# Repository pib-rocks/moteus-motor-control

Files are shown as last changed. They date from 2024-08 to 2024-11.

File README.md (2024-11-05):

# Balancing Lower Body for pib

## Introduction

To aquire stable movement on the ground for pib, we created a wheel leg hybrid to achieve both; fast, energy efficient and manuevarbility of wheels and ability to squat and change posture of legs. For this system, balancing is a fundamental capability to enable stability. In this project, we focus on balancing the lower body of pib, using control algorithms applied to a simplified model of an inverted pendulum on a cart. By implementing control strategies like PID and LQR, we aim to keep the robot upright and stable while moving.

## MJbots MOTEUS

[Moteus](https://github.com/mjbots/moteus) is a high-performance servo motor controller designed by MJBots. It is ideal for robotic applications requiring precise motion control. Moteus offers advanced features such as torque, position, and velocity control, making it suitable for implementing sophisticated control algorithms needed for balancing tasks. We will be using R4.1 controller for this project to control 90kv eagle power brushless motor. The internal control loops for the motor is explained in [PID for motor](https://pib-rocks.atlassian.net/wiki/x/AQBGEg)

## Installation

Clone the repository and navigate to the balancing directory:

```
git clone https://github.com/pib-rocks/moteus-motor-control.git
cd moteus-motor-control/python/balancing
```
Install the required Python packages:
```
pip install -r requirements.txt
```

Configure the motors by running:
```
python3 settings.py
```

## Quick Scripts for LQR and PID Balancing

To quickly test the balancing algorithms on a 1 DOF inverted pendulum system (not on a cart), run the following scripts.
[PID 0 pitch](https://youtube.com/shorts/0coK8HC5Wkk?feature=share)
[LQR 0 pitch](https://youtube.com/shorts/olOWUviZS1A?feature=share)

### PID Balancing

```bash
python3 pid_balancing.py
```

### LQR Balancing

```bash
python3 lqr_balancing.py
```

## Balancing System Explanation

The balancing system models the lower body of PIB as an inverted pendulum mounted on a cart. The cart represents the wheel base, and the pendulum represents the robot's torso. The objective is to apply control inputs to the motors (cart) to keep the pendulum (robot) balanced upright. This setup simplifies the complex dynamics of a humanoid robot to a more manageable control problem. The goal is to keep angular pitch velcoity at 0 and pitch angle upright. To achieve this we are using Tinkerforge IMU bricklet to provide orientation and angular velocity feedback.

## PID Balancing

### PID Controller Explanation
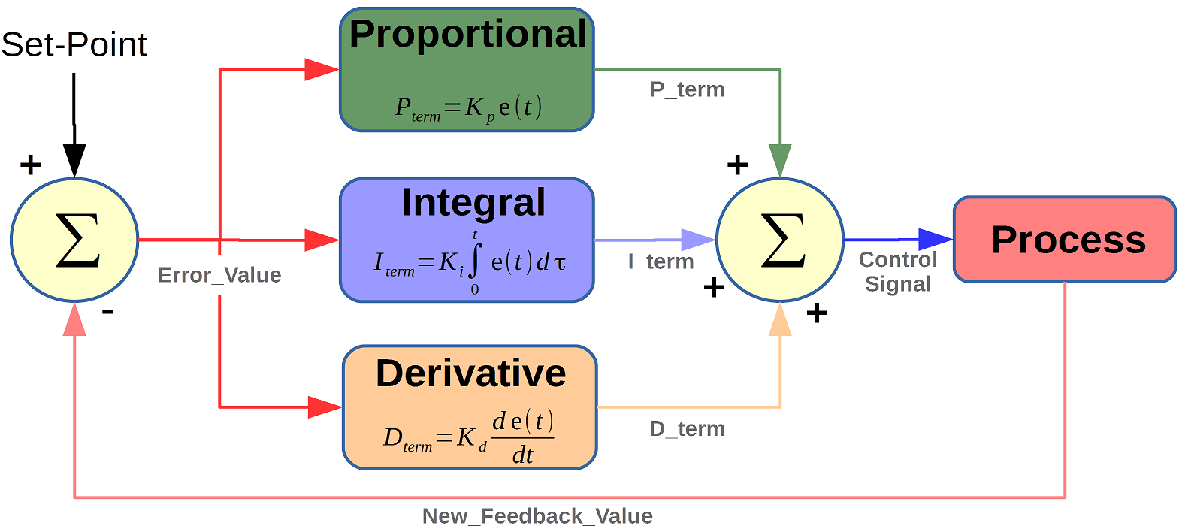
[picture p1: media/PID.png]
PID diagram

A PID controller computes an error value as the difference between a desired setpoint and a measured process variable. It applies a correction based on proportional (P), integral (I), and derivative (D) terms. In our case, we use a PD controller (proportional and derivative terms only) to balance the inverted pendulum.

The control input \( u(t) \) is calculated as:

$$
u(t) = K_p e(t) + K_d \frac{{de(t)}}{{dt}}
$$

- e(t): Error between the desired angle (upright position) and the current angle.
- Kp: Proportional gain.
- Kd: Derivative gain.

The proportional term adjusts the control input proportional to the error, while the derivative term predicts system behavior, providing damping and improving stability. With PID we are running one loop to minimize angular pitch angle to zero by doing velocity control.
videos
[Disturbance compensation with PID](https://youtube.com/shorts/M5Nd9FfMVe8?feature=share)

### Running the PID Script

Execute the PD balancing script:

```bash
python3 pid_balancing.py
```

Ensure that the gains \( K_p \) and \( K_d \) are properly tuned in the script for optimal performance.

## System Dynamics

The inverted pendulum on a cart can be described by the following equations of motion:

$$
m \ddot{x} + m l \ddot{\theta} \cos \theta - m l \dot{\theta}^2 \sin \theta = F
$$

$$
m l \ddot{x} \cos \theta + m l^2 \ddot{\theta} - m g l \sin \theta = 0
$$

Where:
- x: Position of the cart.
- theta: Angle of the pendulum (from vertical).
- m: Mass of the pendulum.
- l: Length to the pendulum's center of mass.
- F: Force applied to the cart.
- g: Acceleration due to gravity.
These nonlinear equations describe the coupling between the cart and pendulum dynamics.

## State-Space Representation

Linearizing the system around the upright position (\( \theta \approx 0 \)), we obtain the state-space representation:
Inverted pendulum cart
$$
\dot{\mathbf{x}} = A \mathbf{x} + B u
$$

$$
\mathbf{y} = C \mathbf{x} + D u
$$

State vector:

$$
\mathbf{x} = \begin{bmatrix} x \\ \dot{x} \\ \theta \\ \dot{\theta} \end{bmatrix}
$$

Input vector:

$$
u = F
$$

System matrices:

$$
A = \begin{bmatrix}
0 & 1 & 0 & 0 \\
0 & 0 & -\frac{m g}{M} & 0 \\
0 & 0 & 0 & 1 \\
0 & 0 & \frac{(M + m) g}{M l} & 0
\end{bmatrix}, \quad
B = \begin{bmatrix}
0 \\
\frac{1}{M} \\
0 \\
-\frac{1}{M l}
\end{bmatrix}
$$

Where:
- M: Mass of the cart.
- m: Mass of the pendulum.
- l: Length to the pendulum's center of mass.
- g: Acceleration due to gravity.
This linearized model is used for designing the LQR controller.

## LQR Balancing

### LQR Controller Explanation
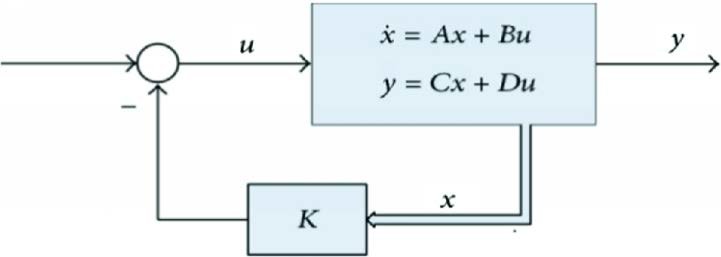
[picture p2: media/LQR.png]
LQR diagram

The Linear Quadratic Regulator (LQR) is an optimal control strategy that minimizes a cost function representing the trade-off between state error and control effort. The cost function is defined as:

$$
J = \int_{0}^{\infty} (\mathbf{x}^\top Q \mathbf{x} + u^\top R u) \, dt
$$

- Q: State weighting matrix (positive semi-definite).
- R: Control input weighting scalar or matrix (positive definite).
- \mathbf{x} \): State vector.
- u: Control input.

The optimal state-feedback gain matrix \( K \) is computed by solving the Continuous-Time Algebraic Riccati Equation (CARE):

$$
A^\top P + P A - P B R^{-1} B^\top P + Q = 0
$$

$$
K = R^{-1} B^\top P
$$

Where \( P \) is the solution to the CARE. The control law becomes:

u = -Kx

[Disturbance compensation with LQR](https://youtube.com/shorts/rGGWK-xfWDU?feature=share)
### Running the LQR Script

Execute the LQR balancing script:

```bash
python3 lqr_balancing.py
```

Ensure that the Q and R matrices are appropriately chosen in the script to balance performance and control effort. Proper tuning of these matrices is crucial for achieving optimal balancing behavior. For simplicity, in the current script there is a variable named "scale_factor" that should be adjusted to scale control output.

## References

- [Josh Pieper: Hoverbot - Hoverboard Motor Balancing Robot](https://youtu.be/syxE1NEU7lw?feature=shared&t=449)

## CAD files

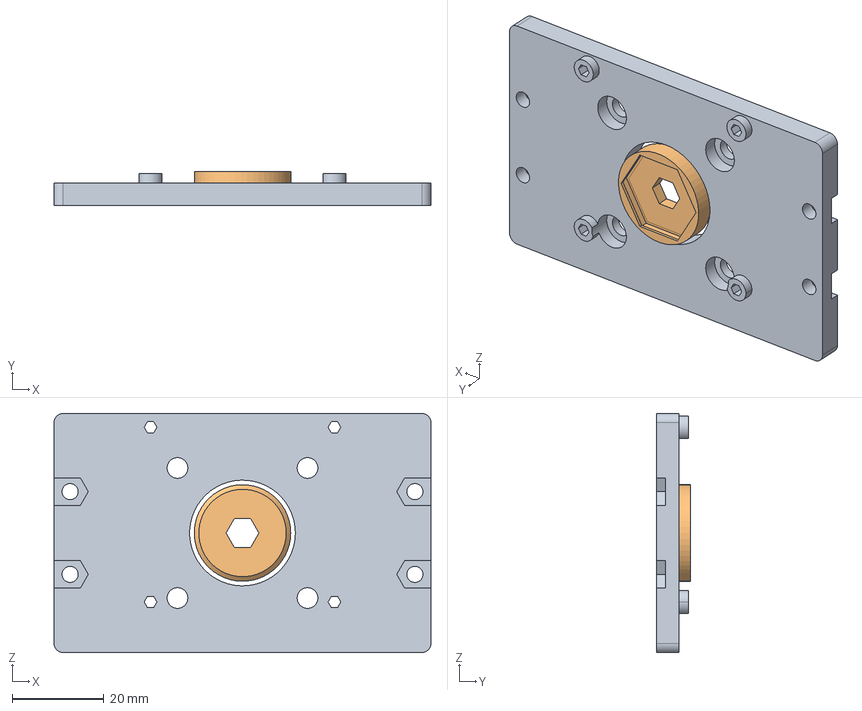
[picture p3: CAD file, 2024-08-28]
freecad/motor-stand/motor-plate.FCStd
82.0 x 7.50 x 52.0 mm
Cap

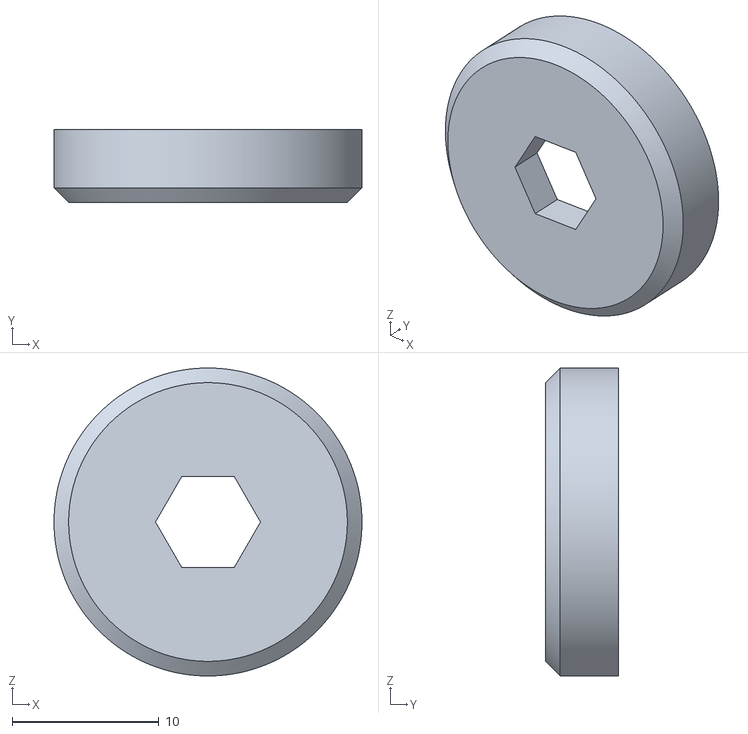
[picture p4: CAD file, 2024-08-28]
freecad/motor-stand/motor-plate-Cap.stl
21.0 x 5.00 x 21.0

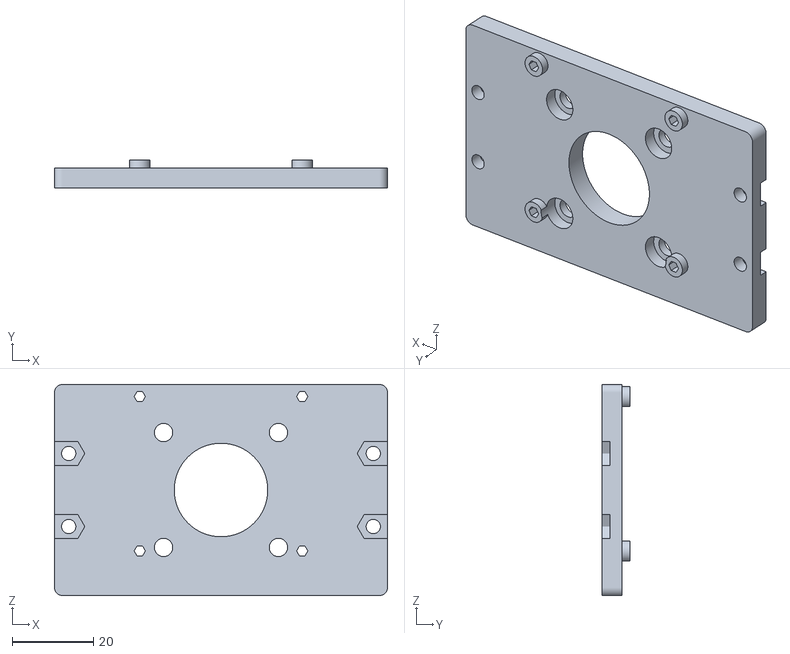
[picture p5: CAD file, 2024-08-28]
freecad/motor-stand/motor-plate-Body.stl
82.0 x 7.00 x 52.0

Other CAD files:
freecad/motor-stand/motor-plate.3mf

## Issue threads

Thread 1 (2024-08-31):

improved parameters for eaglepower direct drive with velocity mode

jnweiger, 2024-08-31:
```
                jw, Sa 31. Aug 17:39:44 CEST 2024

use moteus tview
================

tview -d 1,2 &          # start the gui for motors 1 & 2
# enter velocity mode:
d pos nan 0.5 10 v0.5                   # start rotating slowly 0.5 Hz, with up to 10Nm torque
d pos nan -1 10 v1 a0.5                 # start rotating slowly at 1 Hz backwards, 10 Nm, and accelerate slowly.
conf set servo.max_position_slip 0      # 0 always stops the motor
conf set servo.max_position_slip 1      # allows up to 1 revolution error before we get servo.fault=33 and the motor stops.
conf set servo.max_position_slip nan    # allows up to 1 revolution error before we get servo.fault=33 and the motor stops.
                                        # this depends on the drive direction?? It did not trigger with v=-0.5 ??
d stop && d pos nan -1 10               # clear servo.fault and continue velocity mode.

velocity mode according to video https://youtu.be/dG4fPKN0bas
-------------------------------------------------------------
# do the following for both motors, in the gui, prefix with "1>" (default) and then again with "2>"
conf set servo.max_position_slip 0.2            # unit: revolutions.
                                                #  it only works reliable with non.
conf set servopos.position_max nan
conf set servopos.position_min nan
conf set servo.pid_position.kp 4                # default
conf set servo.pid_position.kd .15              # was 0.04...   .5 also still nice. no overshoot!
conf set servo.pid_position.ki 1                # was 1, not much effect between 0 and 99

conf set servo.default_velocity_limit   ...
conf get servo.default_accel_limit
        5.0
conf set servo.default_accel_limit .5           # so that we can ommit a0.5 from the d pos nan command
# conf limited maximum torque  ? how?
conf set servo.max_position_slip .5             # much stronger torque than with 0.2
#conf set servo.max_position_slip .9            # stronger torque than 0.5, but significant speed overshoot.
conf set servo.max_velocity_slip 9              # unit Hz.

# plot values
servostats.velocity             "measured velocity"
servostats.control_velocity     "internally interpolated velocity that obeys any effective accerlation or velocity limits"
servo_cmd.velocity              "instantaneously updated as commands come in"

conf set servo.pid_position.kp 100              # much stronger
conf set servo.pid_position.kd 3                # 10 rattles
#conf set servo.max_position_slip .1            # good. with kp 100 and kd 3

# emergency stop from the command line:
python3 -m moteus.moteus_tool --target 1 -s

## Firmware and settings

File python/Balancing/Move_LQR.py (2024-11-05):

import asyncio
import time
from tinkerforge.ip_connection import IPConnection
from tinkerforge.bricklet_imu_v3 import BrickletIMUV3
from moteus import Controller
import math
import numpy as np
import control as ct
import threading
import sys

# For keyboard input
import tty
import termios

HOST = "localhost"
PORT = 4223
UID = "2bS8"  # Replace UID

# Global variable for user input
user_velocity = 0.0
user_turn = 0.0

def keyboard_input():
    global user_velocity, user_turn
    # Set terminal to raw mode
    fd = sys.stdin.fileno()
    old_settings = termios.tcgetattr(fd)
    tty.setraw(fd)
    
    try:
        while True:
            key = sys.stdin.read(1)
            if key == 'w':
                user_velocity += 0.1  # Increase forward speed
            elif key == 's':
                user_velocity -= 0.1  # Decrease forward speed
            elif key == 'a':
                user_turn += 0.1      # Turn left
            elif key == 'd':
                user_turn -= 0.1      # Turn right
            elif key == 'q':
                break  # Exit the loop on 'q' key
            else:
                pass  # Ignore other keys
            # Limit the user_velocity and user_turn
            user_velocity = max(min(user_velocity, 1.0), -1.0)
            user_turn = max(min(user_turn, 0.5), -0.5)
    finally:
        # Restore terminal settings
        termios.tcsetattr(fd, termios.TCSADRAIN, old_settings)

async def main():
    global user_velocity, user_turn
    ipcon = IPConnection()
    imu = BrickletIMUV3(UID, ipcon)
    ipcon.connect(HOST, PORT)

    # Initialize controllers
    controller_left = Controller(id=1)
    controller_right = Controller(id=2)

    # System parameters for inverted pendulum on cart
    M = 0.5   # Mass of the cart (kg)
    m = 0.2   # Mass of the pendulum (kg)
    b = 0.1   # Coefficient of friction for cart (N/m/sec)
    I = m * l**2 # Mass moment of inertia of the pendulum (kg*m^2)
    g = 9.81  # Gravity acceleration (m/s^2)
    l = 0.3   # Length to pendulum center of mass (m)

    # Denominator for the A and B matrices
    denom = I*(M+m) + M*m*l**2

    # State-space representation
    A = np.array([
        [0, 1, 0, 0],
        [0, -(I + m * l**2) * b / denom, (m**2 * g * l**2) / denom, 0],
        [0, 0, 0, 1],
        [0, -(m * l * b) / denom, m * g * l * (M + m) / denom, 0]
    ])

    B = np.array([
        [0],
        [(I + m * l**2) / denom],
        [0],
        [m * l / denom]
    ])

    # LQR weighting matrices
    Q = np.diag([10, 1, 10, 1])
    R = np.array([[0.1]])

    # Compute LQR gain
    K, _, _ = ct.lqr(A, B, Q, R)

    # Scale factor to map control input to motor command
    scale_factor = 0.05  # Adjust as necessary

    # Deadband thresholds
    deadband_angle_deg = 0.5  # degrees

    # Start keyboard input thread
    input_thread = threading.Thread(target=keyboard_input)
    input_thread.daemon = True
    input_thread.start()

    print("Starting balancing robot with LQR control and keyboard input. Press 'q' to exit.")

    try:
        while True:
            # Read IMU orientation (pitch angle) and angular velocity
            try:
                _, _, pitch = imu.get_orientation()
                pitch_angle_deg = (pitch / 100.0)*6.3  # Pitch angle in degrees
                pitch_angle_rad = math.radians(pitch_angle_deg)  # Convert to radians

                angular_velocity_x, _, _ = imu.get_angular_velocity()
                # Angular velocity around x-axis (pitch rate), in degrees per second
                pitch_rate_deg_per_sec = angular_velocity_x / 16.0
                pitch_rate_rad_per_sec = math.radians(pitch_rate_deg_per_sec)

                # Assume x and x_dot can be approximated from wheel encoders
                # For simplicity, we set x and x_dot to zero (you can implement odometry here)
                x_pos = 0.0
                x_dot = (controller_left.state.velocity + controller_right.state.velocity) / 2.0
            except Exception as e:
                print(f"Error reading sensors: {e}")
                continue

            # Form state vector x
            x = np.array([
                [x_pos],
                [x_dot],
                [pitch_angle_rad],
                [pitch_rate_rad_per_sec]
            ])

            # Desired state (setpoints)
            x_desired = np.array([
                [0.0],                # Desired position (you can set this to control position)
                [user_velocity],      # Desired velocity (from user input)
                [0.0],                # Desired pitch angle (upright)
                [0.0]                 # Desired pitch rate
            ])

            # Compute control input u using LQR
            u = -K @ (x - x_desired)

            # Extract scalar control input
            command = float(u[0, 0]) * scale_factor


            # Adjust for turning
            left_command = command + user_turn
            right_command = command - user_turn

            # Logging for debugging
            current_time = time.time()
            if int(current_time * 10) % 1 == 0:
                print(f"Pitch Angle: {pitch_angle_deg:.2f}°, Command: {command:.2f}, Left Cmd: {left_command:.2f}, Right Cmd: {right_command:.2f}")

            # Send velocity commands to the motors
            try:
                await controller_left.set_position(
                    position=math.nan,
                    velocity=left_command,
                    velocity_limit=2,
                    maximum_torque=1,
                    kp_scale=1,
                    kd_scale=12
                )
                await controller_right.set_position(
                    position=math.nan,
                    velocity=right_command,
                    velocity_limit=2,
                    maximum_torque=1,
                    kp_scale=1,
                    kd_scale=12
                )
            except Exception as e:
                print(f"Error sending commands to motors: {e}")
                continue

            # Small delay to prevent high CPU usage
            await asyncio.sleep(0.01)

    except KeyboardInterrupt:
        print("Stopping robot...")
    except Exception as e:
        print(f"An unexpected error occurred: {e}")
    finally:
        try:
            await controller_left.set_stop()
            await controller_right.set_stop()
        except Exception as e:
            print(f"Error stopping motors: {e}")
        ipcon.disconnect()

if __name__ == "__main__":
    asyncio.run(main())

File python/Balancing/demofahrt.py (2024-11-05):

#! /usr/bin/python3
#
# References:
#       https://github.com/mjbots/moteus/blob/main/docs/reference.md#velocity-control

import sys
import asyncio
import math
import moteus
import argparse
import time
from numpy import isnan

def custom_usage():
    return f'''Usage: python {sys.argv[0]} [options] <right> <left> <time> <init>

Mandatory arguments:
  right float, revolutions of right motor per seconds. Positive forwards, negative backwards


Optional arguments:
  left float, revolutions of right motor per seconds. Positive forwards, negative backwards. If not provided or nan: Copy value from right
  time float, time in seconds of movement. Default is 3 seconds
  init bool, execute initialization. Default is True 
'''

parser = argparse.ArgumentParser(usage=custom_usage(), add_help=False)

#Optional Arguments
parser.add_argument('--left', type=float, default=math.nan, help='Specify the velocity of left motor')
parser.add_argument('--time', type=float, default=3.0, help='Specify the time of movement in seconds')
parser.add_argument('--init', type=bool, default=True, help='Determine if initialization is needed')

#Mandatory Arguments
parser.add_argument('right', type=float, help='Specify the velocity of right motor')


#Code copied from Moteus example "synchronized movement"
args = parser.parse_args()


#Number of motors
SERVO_IDS = [1,2]

qr = moteus.QueryResolution()
qr.trajectory_complete = moteus.INT8

# Generate controller
controllers = {x: moteus.Controller(x, query_resolution=qr) for x in SERVO_IDS}
# Generate streams (indexed by their espective controller) for commands
streams = {y: moteus.Stream(controllers[y]) for y in controllers}


#main function
#   right: velocity in revolutions per sec for the right wheel, ID = 1
#   left: analogue to right. If left is nan, then the right value will be set
#   time: time of movement. If nan, then endless movement
#   init: initialisation of the motors
async def main(right, left=math.nan, time = 3.0, init = True):
    if init: 
        #delete ristrictions for valid motor positions
        for stream in streams.values(): await stream.command(b"conf set servopos.position_min NaN")
        print("minimum position set to NaN")
        for stream in streams.values(): await stream.command(b"conf set servopos.position_max NaN")
        print("maximum position set to NaN")

        #set PID parameters
        for stream in streams.values(): await stream.command(b"conf set servo.pid_position.kp 20")
        for stream in streams.values(): await stream.command(b"conf set servo.pid_position.ki 1")
        for stream in streams.values(): await stream.command(b"conf set servo.pid_position.kd 1")

        #set max parameters
        for stream in streams.values(): await stream.command(b"conf set servo.max_velocity 8")
        for stream in streams.values(): await stream.command(b"conf set servo.fault_temperature 80")
        
        #if timeout is reached, a stop is necessary for further movements
        for stream in streams.values(): await stream.command(b"d stop")

    #If left is not provided (nan) then copy the value from right
    if isnan(left):
        left = right
    
    #move the right motor (d pos is the command, first paratemer position is nan, second parameter is velocity, third is max torque set to 3, v8 is velocity limit 8, a3 is acceleration limit 3 and t is timeout in second given by time)
    servo_1 = streams[1]
    await servo_1.command(b"d pos nan "+str(right).encode()+b" nan v0.5 a200 t"+str(time).encode())
    #move the left motor
    servo_2 = streams[2]
    await servo_2.command(b"d pos nan "+str(left).encode()+b" nan v0.5 a200 t"+str(time).encode())

if __name__ == '__main__':
    asyncio.run(main(args.right, args.left, args.time, args.init))

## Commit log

2024-08-28 feat: play around with mjbots motor controllers using the moteus python class.
2024-08-28 cad: freecad drawings for the motor stand added.
    [motor-plate-Body.stl, motor-plate-Cap.stl, motor-plate.3mf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]
2024-08-28 review half done: we can timeout a coroutine wiht wait_for, that is not nice, but allows us to send more commands. aborting the servo.set_position with watchdog_timeout had the same effect, but works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
    [demofahrt.py]
2024-08-31 Added temperature limitation and improved PID values
